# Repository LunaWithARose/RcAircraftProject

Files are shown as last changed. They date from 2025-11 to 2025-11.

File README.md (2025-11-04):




# RcAircraftProject

## Frame Version 1

* The first attempted version of my frame.
* 2022-23
* Was never capable of flight
* 6ft wingspan, tapered wings, balsa wood rods, 3d printed filament
* 2x 1300kv brushless motors, 2x 11inch carbon fiber propellers, teensy 4.0, nrf24l01 modules, 5200mah battery
* Main problems included: wingspan sag, tail instability, thin wing chords, lack of electronics space, terrible aerodynamics

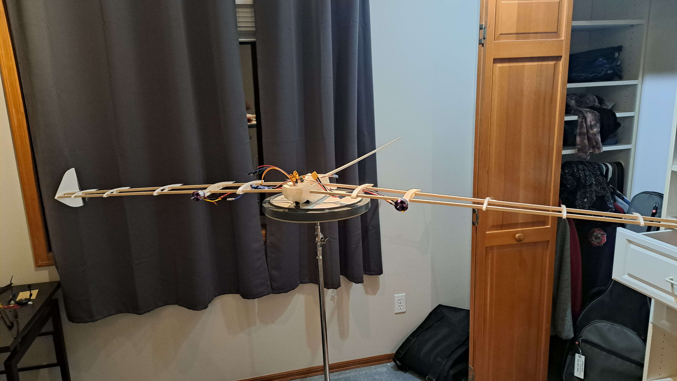
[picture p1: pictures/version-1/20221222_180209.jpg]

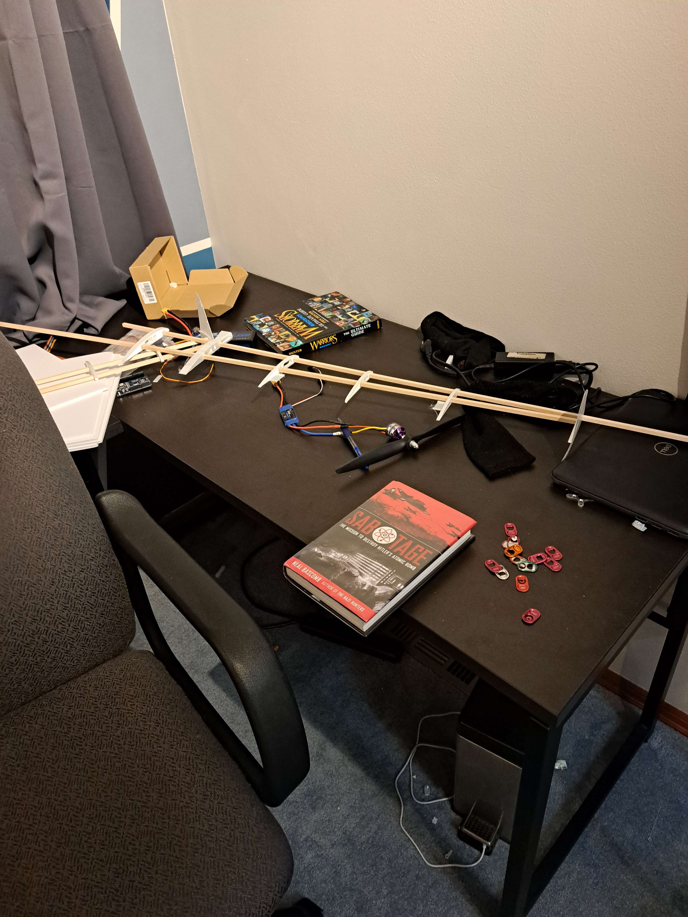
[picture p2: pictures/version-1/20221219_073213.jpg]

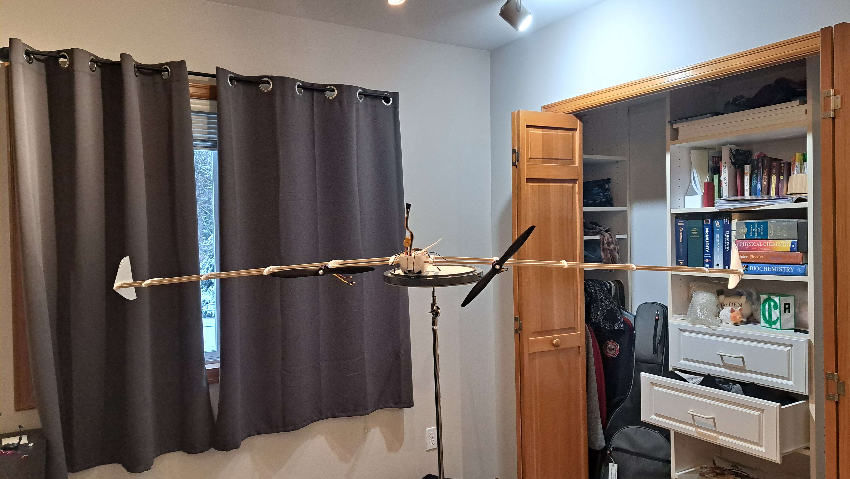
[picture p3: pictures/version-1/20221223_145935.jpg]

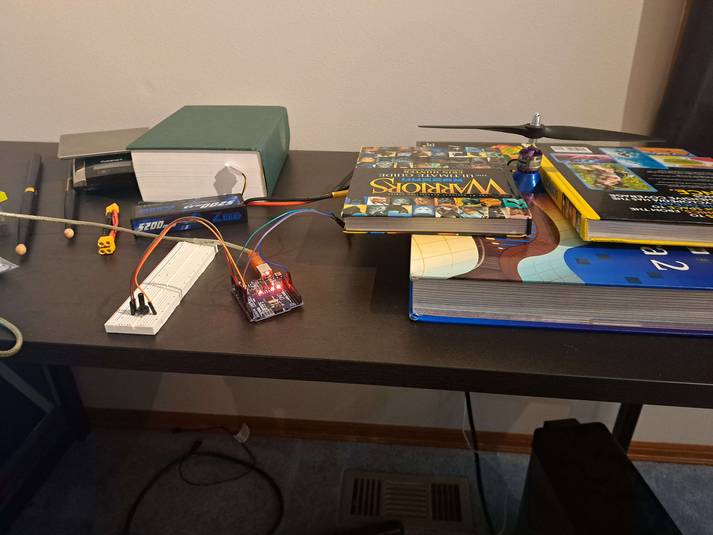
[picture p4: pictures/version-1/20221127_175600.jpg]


## Frame Version 2

* Second Updated version of the frame with many fixes
* 2023-24
* First version of the fram to make an attempted flight
* 8ft wingspan, rectangular wing, balsa wood frame, 3d printed filament
* 2x 1300kv brushless motors, 2x 11inch carbon fiber propellers, teensy 4.0, nrf24l01, 5200mah battery
* Used the 1st and 2nd version of the code
* Fixed problems: significantly better electronics space, larger wing chords, much better aerodynamics, better wing-body connection
* Main problems: still significant wing sag, tail isntability, propeller-motor connection was terrible, nrf24l01 connection was sketchy, centery of gravity & mass was questionable

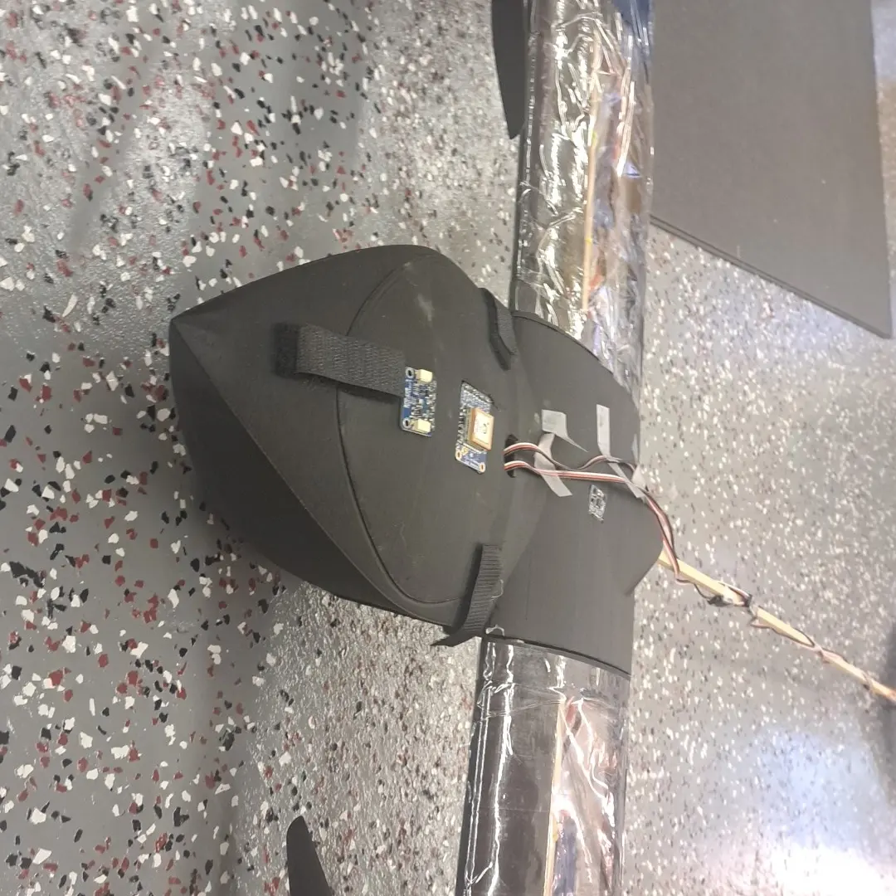
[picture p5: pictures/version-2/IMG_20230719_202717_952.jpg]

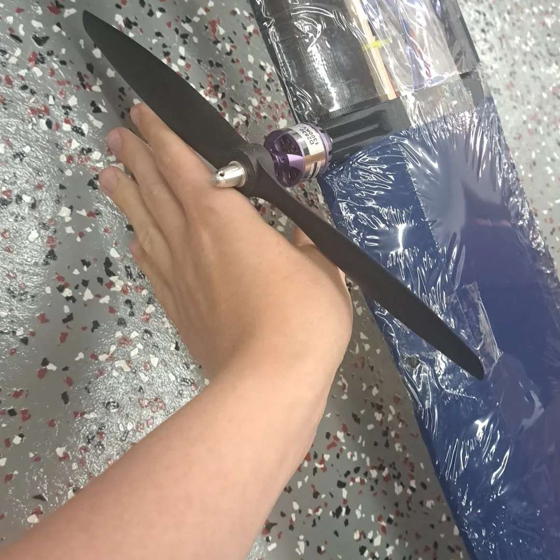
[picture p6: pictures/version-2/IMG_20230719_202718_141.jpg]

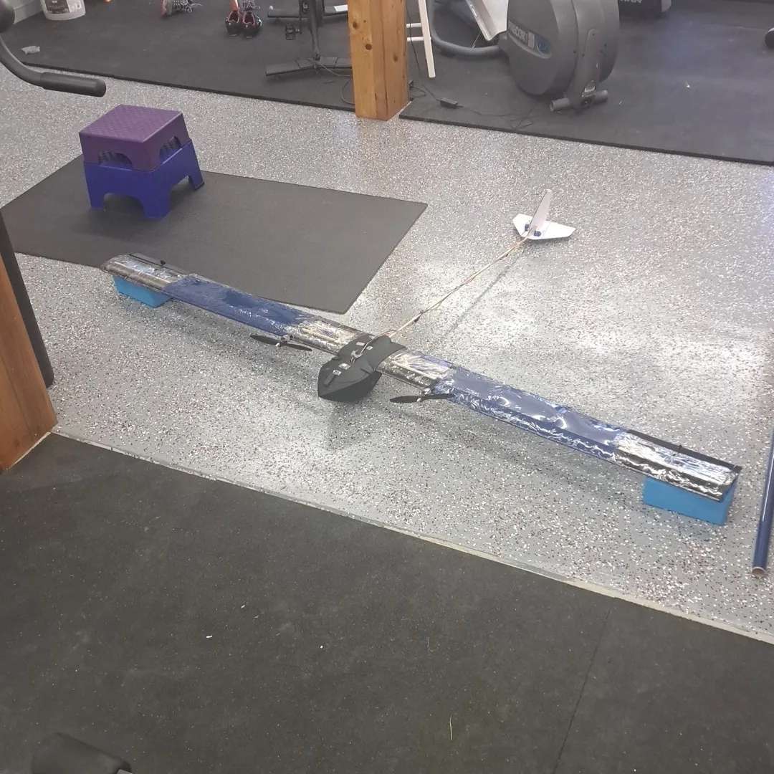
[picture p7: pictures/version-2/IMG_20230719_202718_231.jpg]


## Frame Version 3

* Third and Fourth Version of my frame
* 2024-45
* Most current addition of the airplane. The version that has flew
* 8ft wingspan, rectangular wing, balsawood + carbon fiber frame, 3d printed filament
* 2x 3200kv brushless motos, 2x 8inch carbon fiber propellers, teensy 4.0, nrf24l01+ln+pa, 6900mah battery
* Used the most recent version of code
* Fixed problems: more areo dynamic body, reduced weight, larger but tapered wing chords, significantly less wing sage, tail stability, got more stable nrf24l01 modules, significantly better center of mass & gracvity. Better propeller-motor connection, perfboard cpu

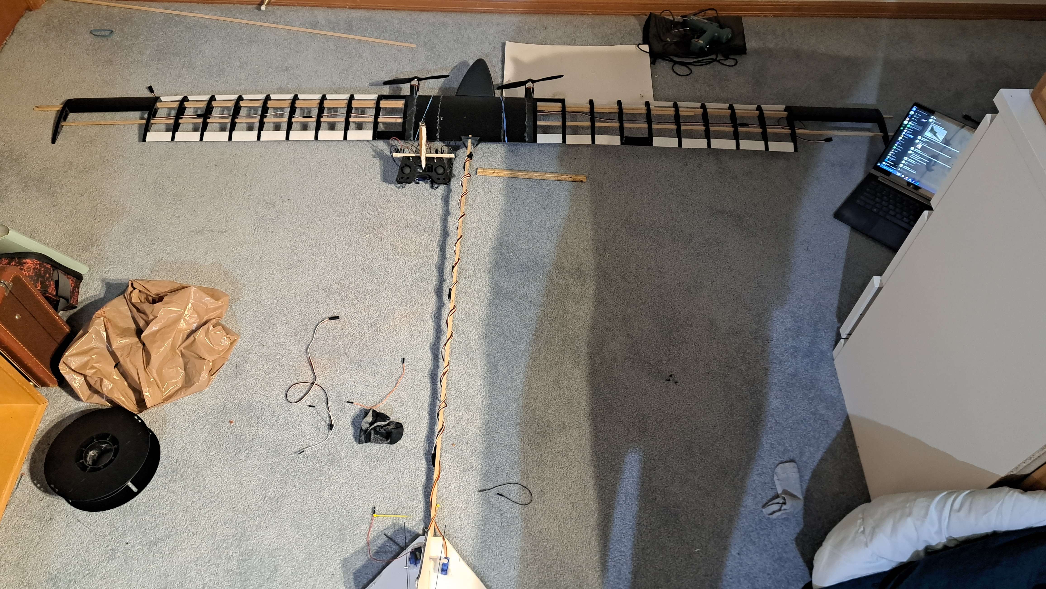
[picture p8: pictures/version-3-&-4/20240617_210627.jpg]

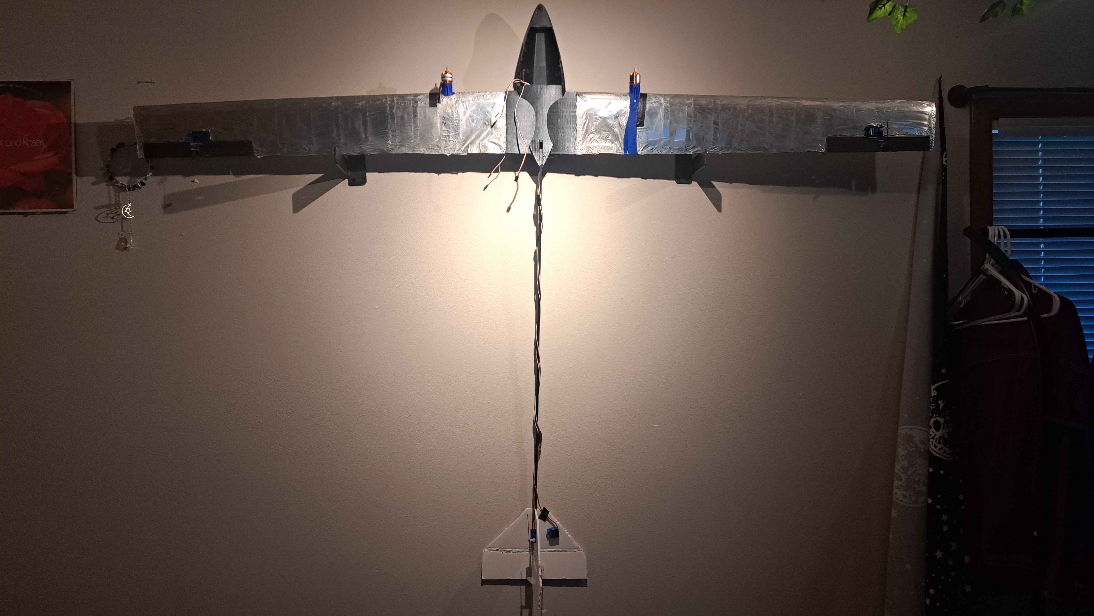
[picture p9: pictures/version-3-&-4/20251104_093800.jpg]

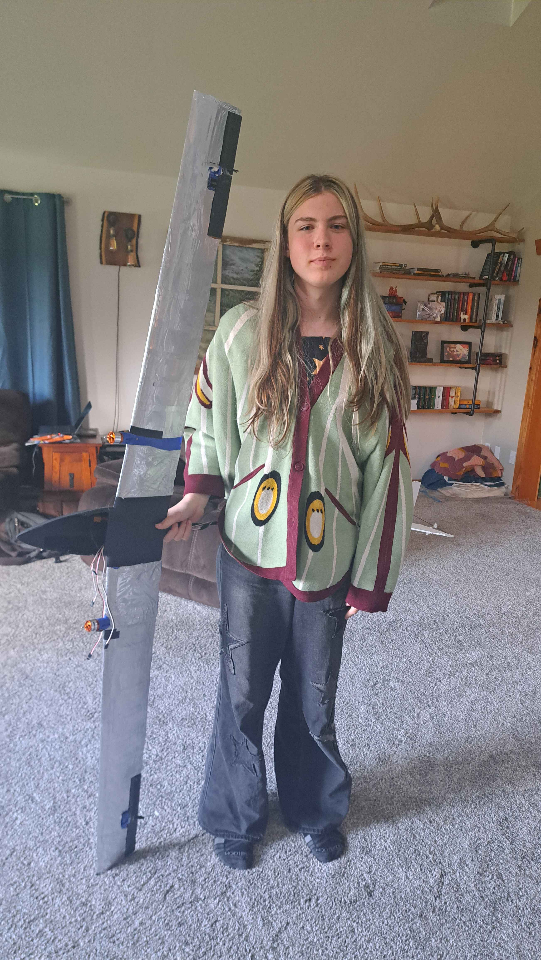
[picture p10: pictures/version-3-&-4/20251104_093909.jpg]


## Boards

Back in 2020-2022 I was super intrested in making pcb boards. I found pictures of two of them. The DRAC had a teensy 4.0 ARM chip as the telemetry and a Arduino ATmel 2650 as the controls system. Each chip had a backup system. The nrf24l01, TinyGPS, and MPU6050 unit on it. There are plenty of other features that I have lost over the past 5 years. I am putting this here to archive it so I do not forget more. 

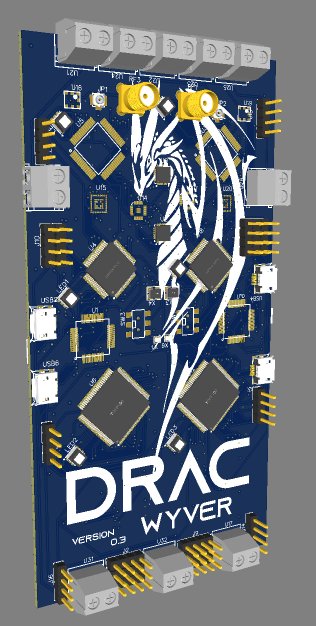
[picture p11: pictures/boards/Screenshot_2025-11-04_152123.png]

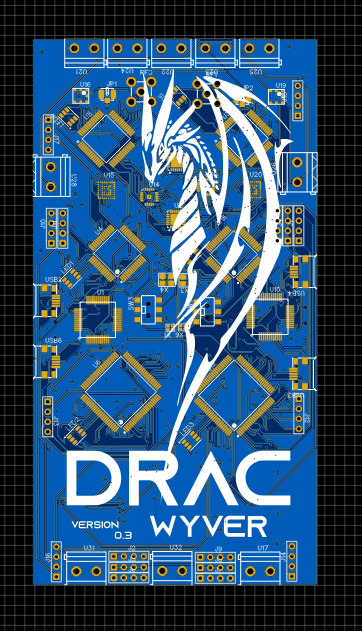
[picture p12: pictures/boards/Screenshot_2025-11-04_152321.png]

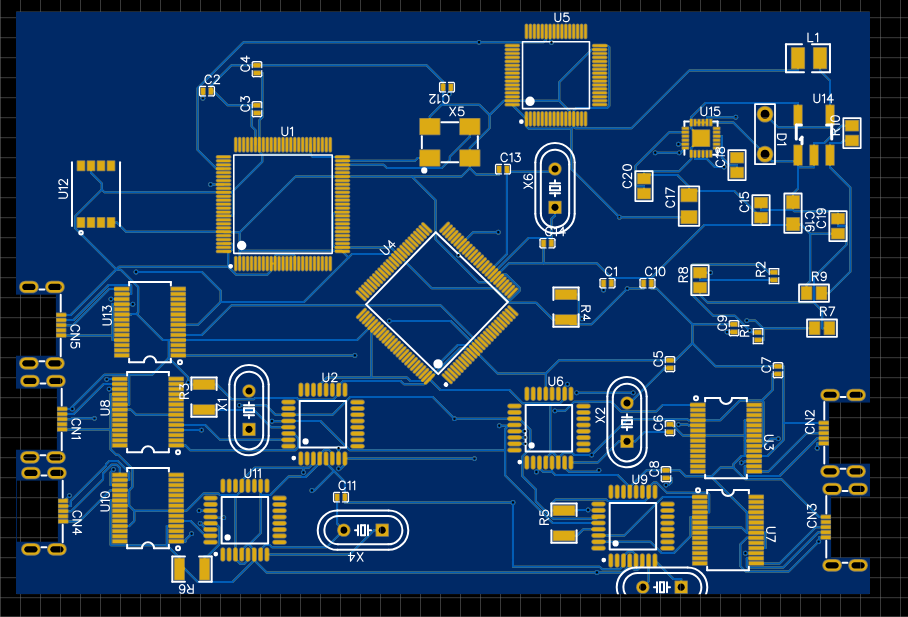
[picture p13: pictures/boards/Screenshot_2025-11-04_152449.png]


The current functioning board that runs in the latest version of my airplane is ran by a teensy 4.0. 

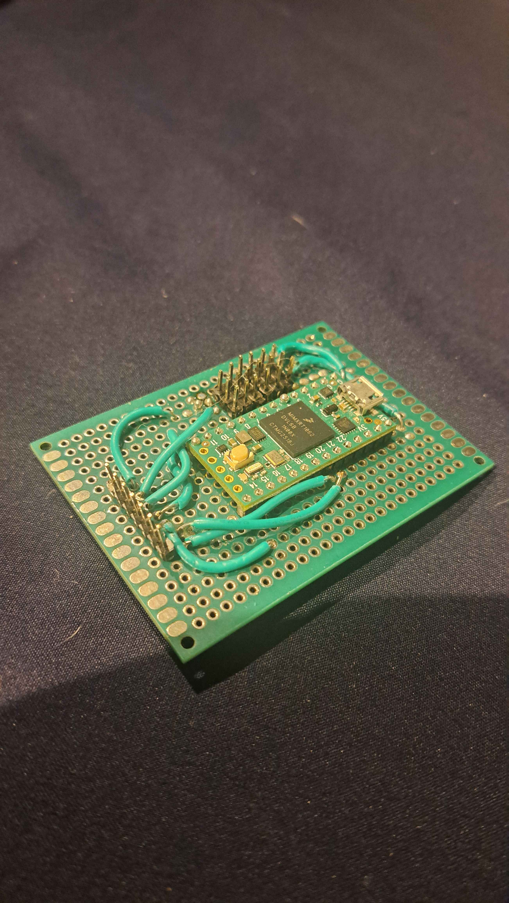
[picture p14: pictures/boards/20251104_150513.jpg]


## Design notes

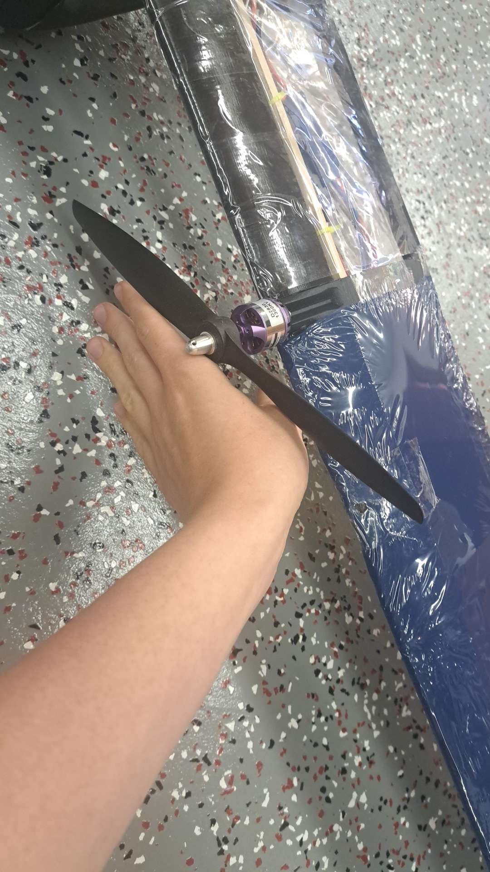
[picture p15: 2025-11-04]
pictures/version-2/Snapchat-404467017.jpg

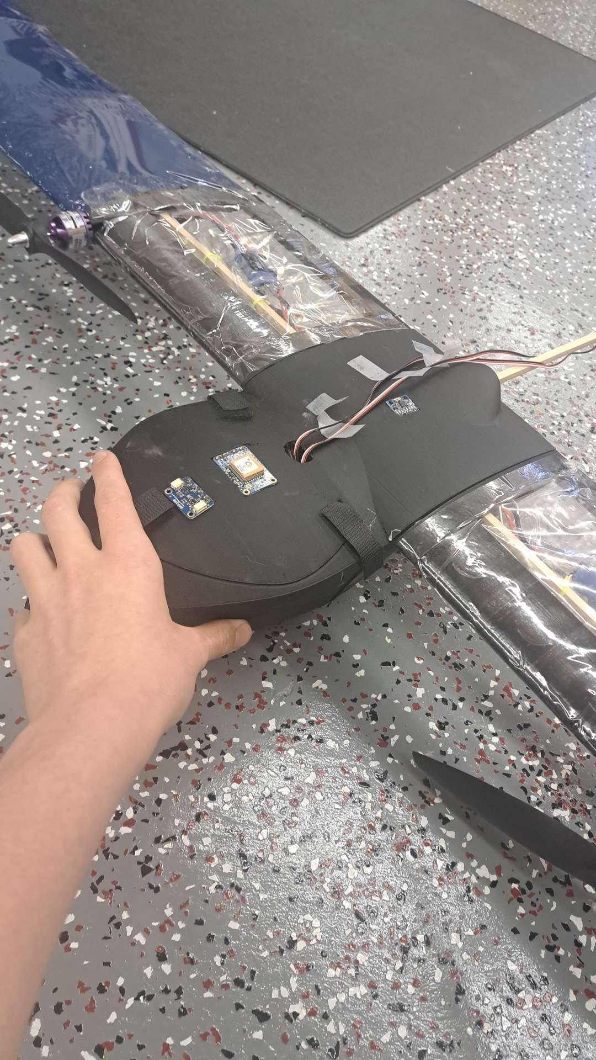
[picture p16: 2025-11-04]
pictures/version-2/Snapchat-1099899814.jpg

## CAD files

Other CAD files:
models/version-1/fusalage v10.f3d
models/version-1/wing v2 v53.f3d
models/version-2/plane v5 v35.f3d
models/version-3/rcplane v19.f3d
models/version-4/rcplane v19.f3d

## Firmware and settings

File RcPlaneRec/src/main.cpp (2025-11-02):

#include <SPI.h>
#include <nRF24L01.h>
#include <RF24.h>
#include <Servo.h>
#include <printf.h>

// Radio
RF24 radio(20, 21); // CE=20, CSN=21
const byte address[6] = "1Node";

// Control payload
struct ControlPayload {
  int16_t aileron;
  int16_t elevator;
  int16_t rudder;
  int16_t throttle;
  uint32_t seq;
};

// Servo objects
Servo aileronServo;
Servo aileronServo2;
Servo elevatorServo;
Servo rudderServo;
Servo esc;
Servo esc2;

unsigned long lastPacket = 0;
const unsigned long FAILSAFE_TIMEOUT = 1000; // 1s

void setup() {
  Serial.begin(115200);
  while (!Serial);

  printf_begin();
  if (!radio.begin()) {
    Serial.println(F("Radio hardware not responding!"));
    while (1);
  }
  radio.setPALevel(RF24_PA_MAX);
  radio.setDataRate(RF24_250KBPS);
  radio.setChannel(76);
  radio.openWritingPipe(address);
  radio.openReadingPipe(1, address);
  radio.startListening();

  // Attach outputs (adjust pins as needed)
  aileronServo.attach(5);
  aileronServo2.attach(6);
  elevatorServo.attach(2);
  rudderServo.attach(3);
  esc.attach(4);
  esc2.attach(7);

  // ESC startup/arming sequence
  Serial.println(F("Arming ESC..."));
  esc.writeMicroseconds(2000);
  esc2.writeMicroseconds(2000);
  delay(2000);
  esc.writeMicroseconds(1000);
  esc2.writeMicroseconds(1000);
  delay(3000);
  Serial.println(F("ESC armed. Waiting for commands..."));

}

void loop() {
  ControlPayload rx;
  bool gotPacket = false;

  if (radio.available()) {
    radio.read(&rx, sizeof(rx));
    lastPacket = millis();
    gotPacket = true;

    // Convert throttle back from -500..500 to 1000..2000 µs
    int throttleOut = map(rx.throttle, -500, 500, 1000, 2000);

    aileronServo.writeMicroseconds(rx.aileron);
    aileronServo2.writeMicroseconds(rx.aileron);
    elevatorServo.writeMicroseconds(rx.elevator);
    rudderServo.writeMicroseconds(rx.rudder);
    esc.writeMicroseconds(throttleOut);
    esc2.writeMicroseconds(throttleOut);

    Serial.print(F("RX seq: "));
    Serial.print(rx.seq);
    Serial.print(F(" | AIL=")); Serial.print(rx.aileron);
    Serial.print(F(" ELEV=")); Serial.print(rx.elevator);
    Serial.print(F(" RUD=")); Serial.print(rx.rudder);
    Serial.print(F(" THR=")); Serial.println(throttleOut);
  }

  // Failsafe – cut throttle if no packets
  if (millis() - lastPacket > FAILSAFE_TIMEOUT) {
    esc.writeMicroseconds(1000); // idle throttle
    Serial.println(F("FAILSAFE: throttle cut"));
  }
}




/*#include <SPI.h>
#include <nRF24L01.h>
#include <RF24.h>
#include <printf.h>

RF24 radio(20, 21); // CE=20, CSN=21

const byte address[6] = "1Node";

struct Payload {
  uint32_t seq;
  uint32_t timestamp;
  char note[16];
};

void setup() {
  Serial.begin(115200);
  while (!Serial);

  printf_begin();
  if (!radio.begin()) {
    Serial.println(F("Radio hardware not responding!"));
    while (1);
  }

  radio.setPALevel(RF24_PA_LOW);
  radio.setDataRate(RF24_1MBPS);
  radio.setChannel(76);
  radio.openWritingPipe(address);
  radio.openReadingPipe(1, address);
  radio.startListening();

  Serial.println(F("Teensy ready, listening..."));
}

void loop() {
  if (radio.available()) {
    Payload rx;
    radio.read(&rx, sizeof(rx));

    Serial.print(F("RX: Got seq="));
    Serial.print(rx.seq);
    Serial.print(F(", note="));
    Serial.println(rx.note);

    // Build reply
    Payload tx;
    tx.seq = rx.seq;
    tx.timestamp = rx.timestamp; // echo back sender's timestamp
    strncpy(tx.note, "PONG from Teensy", sizeof(tx.note));

    radio.stopListening();
    radio.write(&tx, sizeof(tx));
    radio.startListening();

    Serial.println(F("Sent reply"));
  }
}
*/


/*#include "I2Cdev.h"
#include "MPU6050_6Axis_MotionApps20.h"
#include <Wire.h>

MPU6050 mpu;

bool dmpReady = false;
uint8_t devStatus;
uint16_t packetSize;
uint16_t fifoCount;
uint8_t fifoBuffer[64];

Quaternion q;
VectorInt16 aa;
VectorFloat gravity;
float ypr[3];

// Offsets for "zeroing"
float yawOffset = 0;
float pitchOffset = 0;
float rollOffset = 0;

void zeroOrientation() {
  // Grab one valid DMP packet and set as offset
  do {
    fifoCount = mpu.getFIFOCount();
  } while (fifoCount < packetSize);

  mpu.getFIFOBytes(fifoBuffer, packetSize);
  mpu.dmpGetQuaternion(&q, fifoBuffer);
  mpu.dmpGetGravity(&gravity, &q);
  mpu.dmpGetYawPitchRoll(ypr, &q, &gravity);

  yawOffset   = ypr[0];
  pitchOffset = ypr[1];
  rollOffset  = ypr[2];

  Serial.println("Orientation zeroed!");
}

void setup() {
  Wire.begin();
  Wire.setClock(100000);

  Serial.begin(115200);
  while (!Serial);

  Serial.println("Initializing MPU6050...");
  mpu.initialize();

  if (!mpu.testConnection()) {
    Serial.println("MPU6050 connection failed!");
    while (1);
  }

  devStatus = mpu.dmpInitialize();

  // Example hard-coded offsets (replace with calibrated ones later)
  mpu.setXAccelOffset(-1683);
  mpu.setYAccelOffset(-72);
  mpu.setZAccelOffset(1091);
  mpu.setXGyroOffset(37);
  mpu.setYGyroOffset(-14);
  mpu.setZGyroOffset(24);

  if (devStatus == 0) {
    mpu.setDMPEnabled(true);
    dmpReady = true;
    packetSize = mpu.dmpGetFIFOPacketSize();

    Serial.println("DMP ready! Zeroing initial orientation...");
    zeroOrientation();
  } else {
    Serial.print("DMP Initialization failed (code ");
    Serial.print(devStatus);
    Serial.println(")");
  }
}

void loop() {
  if (!dmpReady) return;

  // Check for user input
  if (Serial.available()) {
    char c = Serial.read();
    if (c == 'z' || c == 'Z') {
      zeroOrientation();
    }
  }

  fifoCount = mpu.getFIFOCount();

  if (fifoCount == 1024) {
    mpu.resetFIFO();
    Serial.println("FIFO overflow!");
  } else if (fifoCount >= packetSize) {
    mpu.getFIFOBytes(fifoBuffer, packetSize);

    mpu.dmpGetQuaternion(&q, fifoBuffer);
    mpu.dmpGetGravity(&gravity, &q);
    mpu.dmpGetYawPitchRoll(ypr, &q, &gravity);
    mpu.dmpGetAccel(&aa, fifoBuffer);

    // Apply zero offsets
    float yaw   = (ypr[0] - yawOffset)   * 180/M_PI;
    float pitch = (ypr[1] - pitchOffset) * 180/M_PI;
    float roll  = (ypr[2] - rollOffset)  * 180/M_PI;

    Serial.print("YPR (deg): ");
    Serial.print(yaw);   Serial.print(", ");
    Serial.print(pitch); Serial.print(", ");
    Serial.print(roll);

    Serial.print(" | Accel (g): ");
    Serial.print(aa.x / 16384.0); Serial.print(", ");
    Serial.print(aa.y / 16384.0); Serial.print(", ");
    Serial.println(aa.z / 16384.0);
  }
}


*/


/*
#include <Adafruit_GPS.h>

// Use Serial2 on Teensy 4.0 (RX=7, TX=8)
Adafruit_GPS GPS(&Serial2);

uint32_t timer = millis();

void setup() {
  Serial.begin(115200);
  delay(2000);
  Serial.println("GPS minimal output test...");

  GPS.begin(9600);

  // Only ask for RMC (recommended minimum) + GGA (fix + altitude)
  GPS.sendCommand(PMTK_SET_NMEA_OUTPUT_RMCGGA);
  GPS.sendCommand(PMTK_SET_NMEA_UPDATE_1HZ);   // 1 Hz update
  GPS.sendCommand(PGCMD_ANTENNA);
}

void loop() {
  // Read data from GPS
  char c = GPS.read();

  // Parse NMEA when new sentence is available
  if (GPS.newNMEAreceived()) {
    if (!GPS.parse(GPS.lastNMEA()))
      return;
  }

  // Print once per second when we have a fix
  if (millis() - timer > 1000) {
    timer = millis();

    if (GPS.fix) {
      Serial.print("Lat: ");
      Serial.print(GPS.latitude, 6); Serial.print(GPS.lat);
      Serial.print("  Lon: ");
      Serial.print(GPS.longitude, 6); Serial.print(GPS.lon);

      Serial.print("  Alt: ");
      Serial.print(GPS.altitude); Serial.print(" m");

      Serial.print("  Spd: ");
      Serial.print(GPS.speed * 1.852); Serial.print(" km/h"); // convert knots → km/h

      Serial.print("  Hdg: ");
      Serial.println(GPS.angle);
    } else {
      Serial.println("No GPS fix yet...");
    }
  }
}*/

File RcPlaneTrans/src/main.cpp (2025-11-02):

#include <SPI.h>
#include <nRF24L01.h>
#include <RF24.h>
#include <printf.h>

// Radio
RF24 radio(6, 7); // CE=6, CSN=7
const byte address[6] = "1Node";

// Joystick pins
const int joyLX = A9; // Left stick X (rudder)
const int joyLY = A11; // Left stick Y (throttle)
const int joyRX = A10; // Right stick X (ailerons)
const int joyRY = A8; // Right stick Y (elevator)

// Payload for controls
struct ControlPayload {
  int16_t aileron;
  int16_t elevator;
  int16_t rudder;
  int16_t throttle;
  uint32_t seq;
};

uint32_t seq = 0;

void setup() {
  Serial.begin(115200);
  while (!Serial);

  printf_begin();
  if (!radio.begin()) {
    Serial.println(F("Radio hardware not responding!"));
    while (1);
  }

  radio.setPALevel(RF24_PA_MAX);
  radio.setDataRate(RF24_250KBPS);
  radio.setChannel(76);   // same channel as Teensy
  radio.openWritingPipe(address);
  radio.openReadingPipe(1, address);
  radio.stopListening();

  Serial.println(F("Mega transmitter ready..."));
}

// Map analog stick values to servo range (1000–2000 µs)
int16_t mapJoystick(int raw, bool throttle = false) {
  if (throttle) {
    // Throttle centered at 0, range -500 to +500
    return map(raw, 0, 1023, -180, 180);
  } else {
    // Normal control channels, range 1000–2000
    return map(raw, 0, 1023, 65, 125);
  }
}

void loop() {
  ControlPayload tx;
  tx.seq = seq++;
  tx.aileron = mapJoystick(analogRead(joyRX));
  tx.elevator = mapJoystick(analogRead(joyRY));
  tx.rudder = mapJoystick(analogRead(joyLX));
  tx.throttle = mapJoystick(analogRead(joyLY), true);

  bool ok = radio.write(&tx, sizeof(tx));
  if (ok) {
    Serial.print(F("Sent seq: "));
    Serial.print(tx.seq);
    Serial.print(F(" | AIL=")); Serial.print(tx.aileron);
    Serial.print(F(" ELEV=")); Serial.print(tx.elevator);
    Serial.print(F(" RUD=")); Serial.print(tx.rudder);
    Serial.print(F(" THR=")); Serial.println(tx.throttle);
  } else {
    Serial.println(F("Send failed"));
  }

  delay(50); // ~20Hz updates
}




/*
#include <SPI.h>
#include <nRF24L01.h>
#include <RF24.h>
#include <printf.h>

RF24 radio(6, 7); // CE=5, CSN=6

const byte address[6] = "1Node";

struct Payload {
  uint32_t seq;
  uint32_t timestamp;
  char note[16];
};

uint32_t seq = 0;

void setup() {
  Serial.begin(115200);
  while (!Serial);

  printf_begin();
  if (!radio.begin()) {
    Serial.println(F("Radio hardware not responding!"));
    while (1);
  }

  radio.setPALevel(RF24_PA_LOW);
  radio.setDataRate(RF24_1MBPS);
  radio.setChannel(76);
  radio.openWritingPipe(address);
  radio.openReadingPipe(1, address);
  radio.stopListening();

  Serial.println(F("Mega ready, sending..."));
}

void loop() {
  Payload tx;
  tx.seq = seq++;
  tx.timestamp = millis();
  strncpy(tx.note, "PING from Mega", sizeof(tx.note));

  Serial.print(F("TX: Sending seq="));
  Serial.print(tx.seq);

  bool ok = radio.write(&tx, sizeof(tx));
  if (ok) Serial.println(F(" ... sent OK"));
  else Serial.println(F(" ... failed"));

  // Listen briefly for reply
  radio.startListening();
  unsigned long started = millis();
  bool timeout = false;

  while (!radio.available() && !timeout) {
    if (millis() - started > 200) timeout = true;
  }

  if (timeout) {
    Serial.println(F("No reply"));
  } else {
    Payload rx;
    radio.read(&rx, sizeof(rx));
    uint32_t rtt = millis() - rx.timestamp;

    Serial.print(F("RX reply: seq echo="));
    Serial.print(rx.seq);
    Serial.print(F(", age(ms)="));
    Serial.print(rtt);
    Serial.print(F(", note="));
    Serial.println(rx.note);
  }

  radio.stopListening();
  delay(1000);
}
*/
